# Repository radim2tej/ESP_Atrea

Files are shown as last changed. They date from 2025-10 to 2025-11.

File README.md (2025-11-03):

# ESP Atrea #
Replacement of the CP 07 RD controller with the ESP8266 module for controlling the Atrea RB / RC / RK2 / RDH air handling units and similar using Home Assistant. The module can either monitor or directly replace the CP07 controller via ESP8266, LIN bus interface and a Home Assistant. The module allows control of ventilation, heating and cooling.
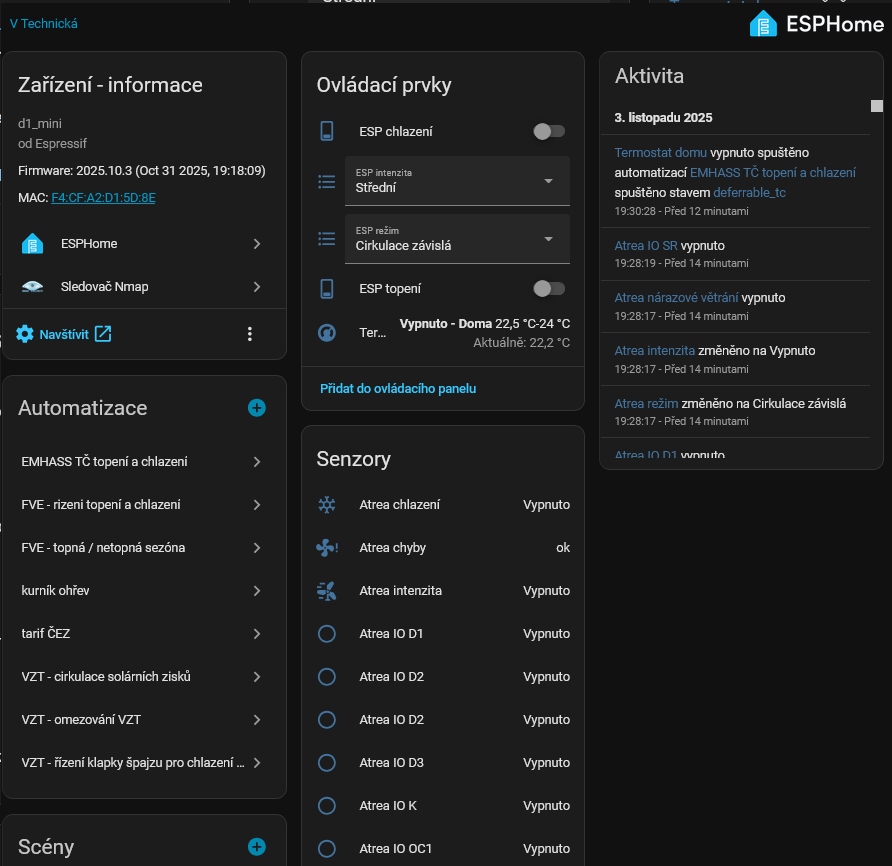
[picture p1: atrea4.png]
device


# Hardware
The CP07 controller communicates with the ATREA RK2 heat recovery unit via the LIN bus. It communicates at 300 Bauds and each packet has 10 bytes. The CP07 controller sends a query to the Atrea unit (the type is in bytes 2 and 3) and receives a response from Atrea.

For the connection use a LIN bus interface [TTL UART to LIN Can Bus Converter](https://www.aliexpress.com/item/1005006301070554.html) or maybe [UART to LIN Bus Module](https://www.aliexpress.com/item/1005008689817215.html), an ESP8266 module WeMos D1 mini and [DC Power Shield V1.1.0 for WEMOS D1 mini](https://www.aliexpress.com/item/1005001621800502.html).
The ESPAtrea module can completely replace the CP07 controller, but I recommend only inserting the module into the wiring and disconnecting the LINBUS wire to the CP07 controller with a switch due to the possibility of setting parameters. If the CP07 controller is connected and communicating, the ESPAtrea module detects this and only monitors the communication. The CP07 driver is still required to configure the unit, but can be disconnect after setup ATREA.

The complete module can be installed in a [printed box](espatrea.stl) with WAGO terminals. There is also space for installing a LINBUS switch for CP07.

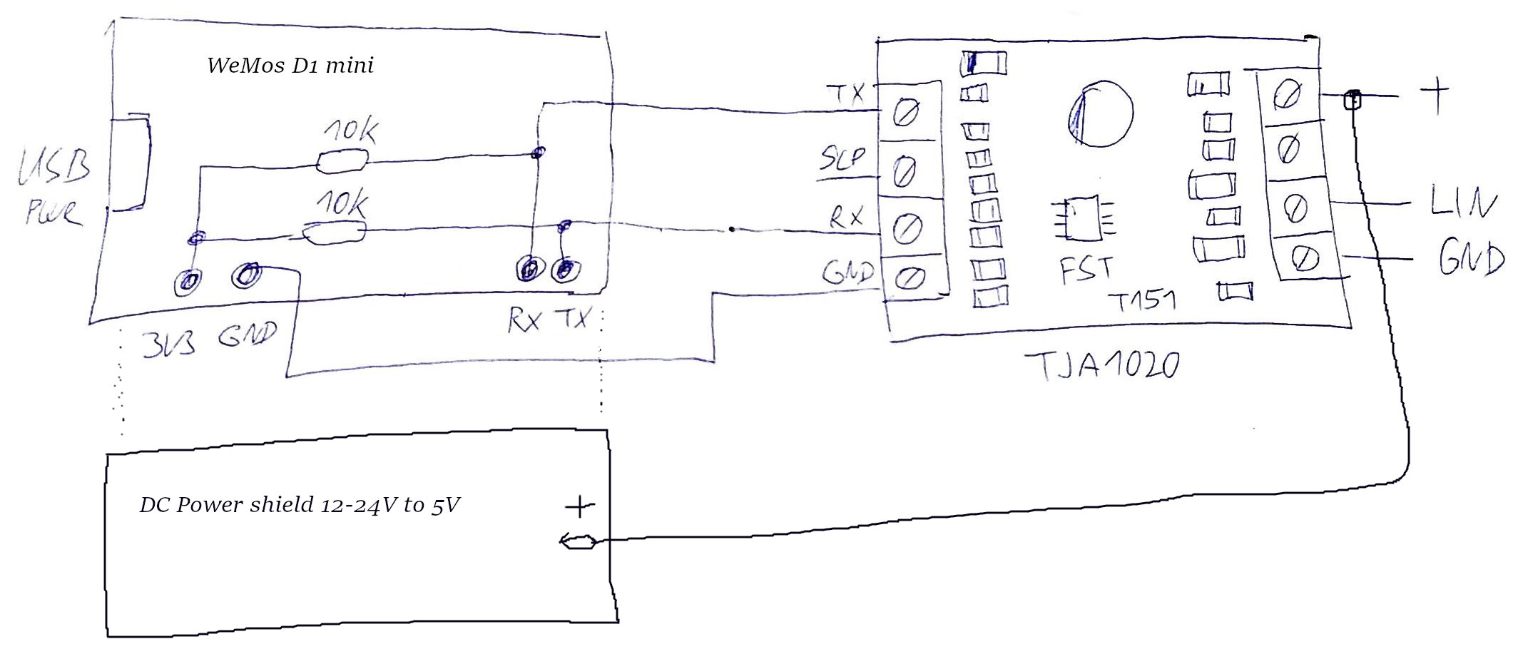
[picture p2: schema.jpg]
schema

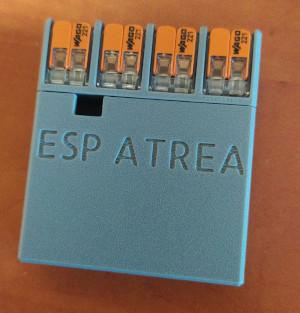
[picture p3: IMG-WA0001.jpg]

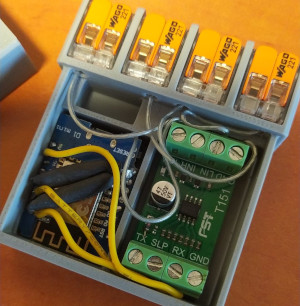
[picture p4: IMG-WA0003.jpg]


# Logs CP07 (fw 54.07) <-> Atrea (PIC fw 53.59 for Heating pump)
[Logs for individual modes](log.md)

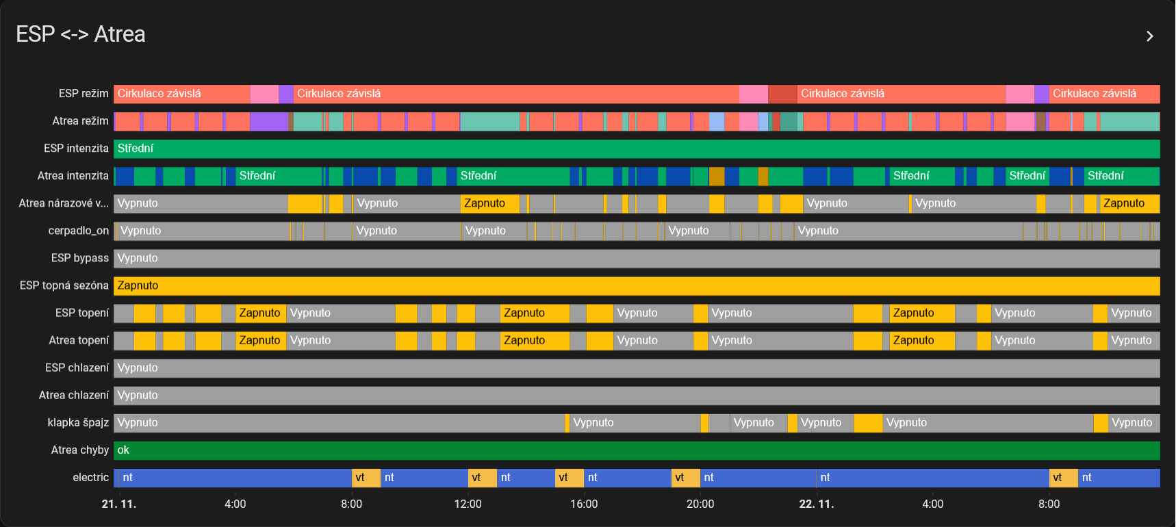
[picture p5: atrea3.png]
panel 1


# Decode packets
### The requests packet from the CP07 controller to the Atrea unit:
- 0xF5 [id1 0,1,2] [id2 1,3] [intensity 1,2,4] [mode 1,2,4,8,16] [bps 1,2] [md 1,2] [temp 0,1,2,3] 0x00 [crc]
  - id1 and id2: 0 1, 0 3, 1 3, 2 3
  - intensity is 1=off, 2=medium or 4=max
  - modes:
    - pressure ventilation (PV): mode = 1, bps = 2, md = 1, temp = 0
    - circulation (C): mode = 4, bps = 2, md = 1, temp = 0,2,3
    - dependent circulation (CZ): mode = 4, bps = 2, md = 2, temp = 0,2,3
    - circulation ventilation (CV): mode = 8, bps = 1,2, md = 1, temp = 0,2,3
    - equal pressure ventilation (RV): mode = 16, bps = 1,2, md = 1, temp = 0,2,3
    - cooling: mode = 1, bps = 2, md = 2, temp = 0,1
  - bps: bypass flap for RV and CV (1 bypass, 2 recuperator), in other modes is 2 
  - temp: bit 0x01 = heating / cooling, bit 0x02 = heating season (for new fw CP07?)

- 0xF5 [id1 0x41,0x42,0x43] [id2 0x01] [circulation flap DA1] [node DA2] [MC] [MV] [bits] 0x00 [crc]
  - simul. voltage intake circulation flap DA1: 0-255=0V-10V (adding fresh air 0-0%, 255-100%)
  - simul. voltage node DA2: 0-255=0V-10V
  - engine MC: 0,1,2,3
  - engine MV: 0,1,2
  - bits: 1=bypass SB, 2=ground cooler/intake flap SR (for input E1), 4=pump YV (heat pump heating), 8=electric/gas boiler K, 16=output OC1 (heat pump cooling), 32=output EXT

### The responds packet with the same id1 and id2 from the Atrea unit to the CP07 controller:
- 0xF5 [id1 0x00] [id2 0x01] [mode2 0,1,2,4,5,8,16] [flags: intensity 0,1,2, errorB 0x04, heating 0x08, shock vent. 0x10, fx 0x20] [errors] [TE] [TA] x [crc]
  - modes:
    - nothing: mode2 = 0, flags = 0 or 0x20
    - pressure ventilation: mode2 = 1, flags = 1 or 2
    - circulation: mode2 = 4, flag = 1 or 2
    - dependent circulation standby: mode2 = 4, flags = 0x20
    - dependent circulation ventilation: mode2 = 8, flags = 0x21 or 0x22
    - circulation ventilation: mode2 = 8, flag = 1 or 2xxx
    - equal pressure ventilation: mode2 = 16, flag = 0x21 or 0x22 (electric/gas boiler heating)
    - cooling: mode2 = 5, flags = 0x21 or 0x22
    - heating: mode2 = 4 (circulation dep. and circulation), 8 (circulation vent.), 16 (equal press. vent.), flags = 1 or 2 + 0x08 + fx
  - intensity: 0=off, 1=medium or 2=max
  - shock ventilation flag 0x10 (0x31 or 0x32 with intensity 1 or 2)
  - fx: RV 0 or 0x20 (keeps the previous state), CV 0 or 0x20 (keeps the previous state), CZ 0x20, C 0, PV 0, Cooling 0x20
  - errorB: 0x04 = filter clogged
  - errors: 1=TE error, 2=TI2 error, 4=recuperator freezing, 8=TA error, 16=1st.freezing protection (TI2 < 12°C), 32=2nd.freezing protection (TI2 < 7°C), 64=active STOP, 128=communication error
  - outdoor temperature = TE-50
  - radiator temperature = TA-50

- 0xF5 [id1 0x00] [id2 0x03] [0x60 + power inputs D1-D4 1,2,4,8] [mode] [i1 0x00] [i2 0x00] [i3 0x00] [bits] [crc]
  - power inputs: D1-D3 WC and bathroom 1,2,4, D4 kitchen 8, D11 ?
  - mode: 0=off, 2=PV medium or C medium, 3=PV max or C max, 5=RV medium, 10=RV max or shock ventilation, 6=CV medium, 7=CV max
  - i1-i3: I thing voltage in1-in3 0-255=0V-10V
  - bits: 1=ground cooler/intake flap SR (for input E1), 2=bypass SB, 4=pump YV (heat pump heating), 8=electric/gas boiler K, 32=output OC1 (heat pump cooling)
 
- 0xF5 [id1 0x01] [id2 0x03] [circulation flap DA1] [TA] [TI2] [TE] 0x00 0x99 [crc]
  - intake circulation flap DA1 0-255=0V-10V (adding fresh air 0-0%, 255-100%)
  - radiator temperature = TA-50
  - behind recuperator temperature = TI2-50
  - outdoor temperature = TE-50

- 0xF5 [id1 0x02] [id2 0x03] 0xFF 0x33 0x82 0xEC 0xFF 0xCB [crc]
  
- 0xF5 [id1 0x41] [id2 0x01] [TA] [TI2] [TE] 0x00 0x00 0x00 [crc]
  - radiator temperature = TA
  - behind recuperator temperature = TI2
  - outdoor temperature = TE
      
- 0xF5 [id1 0x42] [id2 0x01] 0xFF 0x33 0x82 0xEC 0xFF 0x0B [crc]
  
- 0xF5 [id1 0x43] [id2 0x01] 0x03 [D1..4] 0x00 0x00 0x00 0x00 [crc]
  - D1..4: D1-D3 WC and bathroom 2,4,8, D4 kitchen 16

### Byte bps control with CP07 controller
The Bps byte control the bypass flap - 1 for bypass and 2 for recuperator. In RV and CV mode, the CP07 controller sets the byte bps according to the outdoor TE temperature, room temperature, and target setpoint temperature. In other modes, the byte bps is set to 2.
#### Rules:
- for a heating season and active heating the CP07 controller sets bps to 2 
- for the heating season, not heating and RV mode
  - 1 = the outdoor TE temperature is greater or equal than 18°C and both the outdoor TE temperature and the requested indoor temperature are less than the actual room temperature
  - 2 = the outdoor TE temperature is less than 17°C or the outdoor TE temperature is greater than the actual room temperature or the requested indoor temperature is greater than the actual room temperature
- for the heating season, not heating and CV mode
  - 1 = the outdoor TE temperature is greater or equal than 16°C and both the outdoor TE temperature and the requested indoor temperature are less than the actual room temperature
  - 2 = the outdoor TE temperature is less than 15°C or the outdoor TE temperature is greater than the actual room temperature or the requested indoor temperature is greater than the actual room temperature
- for the non-heating season and RV mode
  - 1 = the outdoor TE temperature is greater or equal than 16°C and both the outdoor TE temperature and the requested indoor temperature are less than the actual room temperature
  - 2 = the outdoor TE temperature is less than 15°C or the outdoor TE temperature is greater than the actual room temperature or the requested indoor temperature is greater than the actual room temperature
- for the non-heating season and CV mode
  - 1 = the outdoor TE temperature is greater or equal than 13°C and both the outdoor TE temperature and the requested indoor temperature are less than the actual room temperature
  - 2 = the outdoor TE temperature is less than 12°C or the outdoor TE temperature is greater than the actual room temperature or the requested indoor temperature is greater than the actual room temperature

# Instalation
Programming of the module uses the ESPHome 2025 environment. The code is written in C and in YAML (espatrea.yaml and files in components/atrea). The files are moved to configuration/esphome. The wifi password is in secrets.yaml . In espatrea.yaml, edit the API Key and OTA and Wifi passwords. The module contains a software dual thermostat, and the current temperature is set by the home assistant via the sensor sensor.teplota_termostatu. The thermostat controls the switches switch.esp_topení and switch.esp_chlazeni.

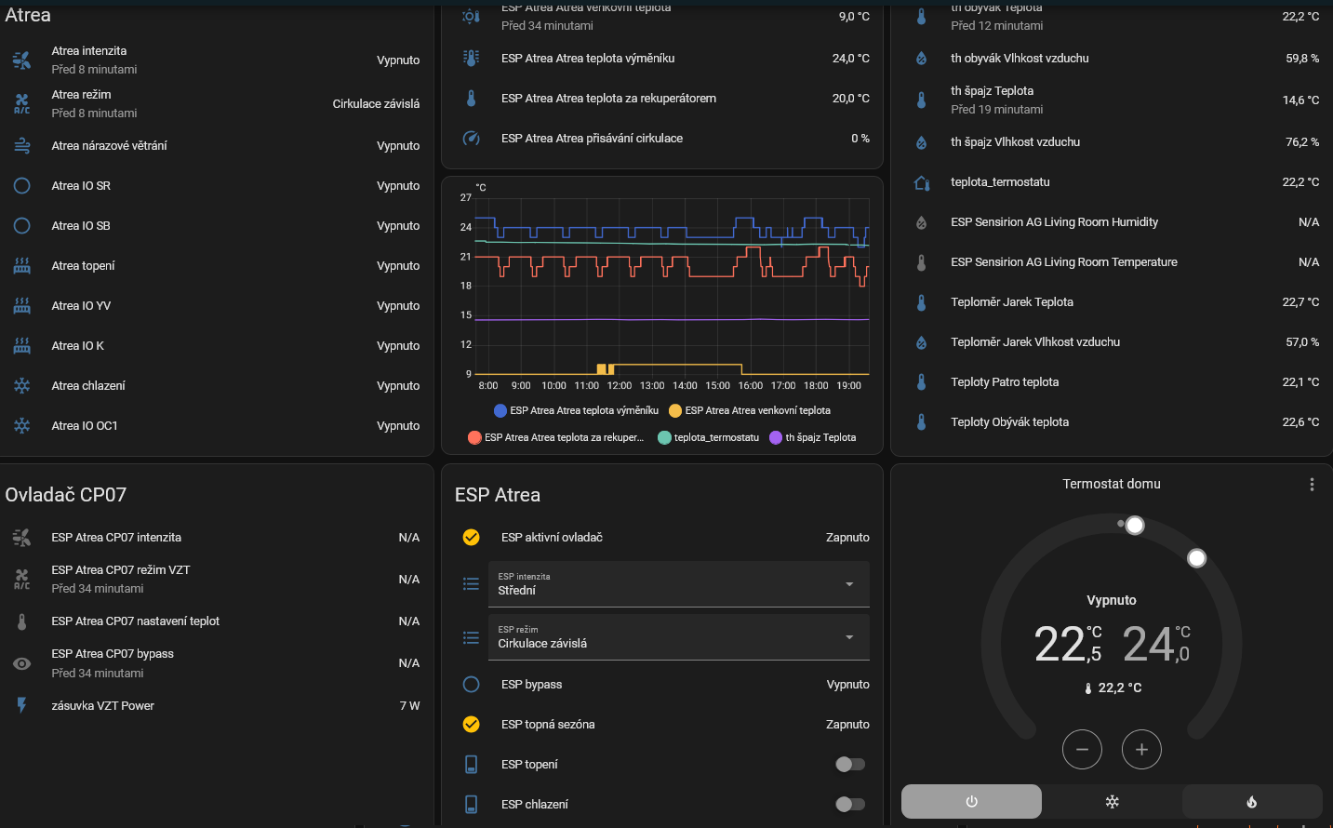
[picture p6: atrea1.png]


The unit modes can be selected via select.esp_rezim_vzt and select.esp_intenzita, and you can use scheduler to change modes due to different programs for individual days. Usually the unit runs in CZ mode, switches to RV in the morning and then to CV. Then it runs in CZ mode until the evening and then switches to RV, then to C and then to CZ. It varies by day of the week.

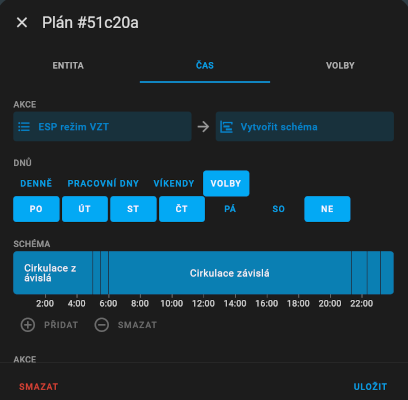
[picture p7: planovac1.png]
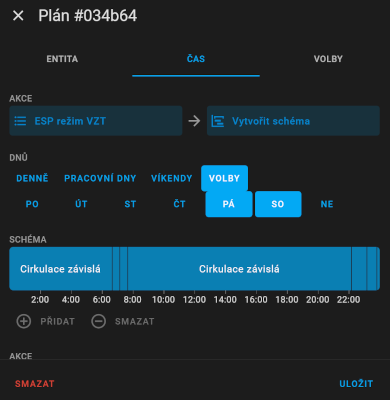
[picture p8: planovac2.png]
 

# Examples of automations
Solar gain circulation
```
alias: VZT - cirkulace solárních zisků
description: ""
triggers:
  - entity_id:
      - sun.sun
    attribute: elevation
    trigger: state
  - entity_id: sensor.pv_power
    for:
      hours: 0
      minutes: 10
      seconds: 0
    above: 2500
    enabled: false
    trigger: numeric_state
conditions:
  - condition: numeric_state
    entity_id: sun.sun
    attribute: elevation
    above: 14
actions:
  - if:
      - condition: numeric_state
        entity_id: sun.sun
        attribute: elevation
        above: 16
      - condition: numeric_state
        entity_id: climate.termostat_domu
        attribute: target_temp_high
        below: sensor.teplota_termostatu
    then:
      - action: select.select_option
        metadata: {}
        data:
          option: Cirkulace
        target:
          entity_id: select.esp_rezim_vzt
      - action: select.select_option
        metadata: {}
        data:
          option: Maximální
        target:
          entity_id: select.esp_intenzita
    else:
      - action: select.select_option
        metadata: {}
        data:
          option: Cirkulace závislá
        target:
          entity_id: select.esp_rezim_vzt
      - action: select.select_option
        metadata: {}
        data:
          option: Střední
        target:
          entity_id: select.esp_intenzita
mode: single
```

Control heating and cooling
```
alias: VZT - rizeni topení a chlazení
description: >-
  VZT nastavování teploty topení, blokování topení podle ceny, chlazení při
  nadbytku FVE
trigger:
  - platform: state
    entity_id:
      - sensor.final_price_kwh
    for:
      hours: 0
      minutes: 0
      seconds: 0
  - platform: state
    entity_id:
      - binary_sensor.atrea_narazove_vetrani
  - platform: time_pattern
    minutes: /20
    seconds: "5"
action:
  - alias: topení
    if:
      - condition: state
        entity_id: climate.termostat_domu
        state: heat
    then:
      - if:
          - condition: or
            conditions:
              - condition: state
                entity_id: binary_sensor.count_offpeak_heat_cheapest_hours
                state: "on"
              - condition: state
                entity_id: binary_sensor.count_peak_heat_cheapest_hours
                state: "on"
        then:
          - action: climate.set_temperature
            metadata: {}
            data:
              target_temp_low: 22
              target_temp_high: 24
            target:
              entity_id: climate.termostat_domu
        else:
          - if:
              - condition: state
                entity_id: binary_sensor.count_expensive_hours
                state: "on"
            then:
              - action: climate.set_temperature
                metadata: {}
                data:
                  target_temp_low: 20.5
                  target_temp_high: 24
                target:
                  entity_id: climate.termostat_domu
            else:
              - action: climate.set_temperature
                metadata: {}
                data:
                  target_temp_low: 21.5
                  target_temp_high: 24
                target:
                  entity_id: climate.termostat_domu
    else:
      - alias: kontrola nadbytku energie pro chlazeni
        if:
          - condition: and
            conditions:
              - condition: or
                conditions:
                  - condition: numeric_state
                    entity_id: sensor.pv_power
                    above: 2800
                  - condition: numeric_state
                    entity_id: sensor.export_s_tc
                    above: 900
              - condition: numeric_state
                entity_id: sensor.battery_state_of_charge
                above: 50
              - condition: numeric_state
                entity_id: sensor.solcast_pv_forecast_forecast_remaining_today
                below: sensor.battery_state_of_charge
                value_template: >-
                  {{ max(130 - 100 *
                  states('sensor.solcast_pv_forecast_forecast_remaining_today')
                  | float(default=50.0) / 14.4, 0) }}
                alias: bude větší výroba energie FVE k dobití baterie do 100%
              - condition: state
                entity_id: binary_sensor.chladici_sezona
                state: "on"
        then:
          - data:
              hvac_mode: cool
            target:
              entity_id: climate.termostat_domu
            action: climate.set_hvac_mode
          - device_id: 904cd0b7d9147d7b3b4ad392bb80d9a8
            domain: select
            entity_id: select.esp_intenzita
            type: select_option
            option: Maximální
            enabled: false
        else:
          - data:
              hvac_mode: "off"
            target:
              entity_id: climate.termostat_domu
            action: climate.set_hvac_mode
          - device_id: 904cd0b7d9147d7b3b4ad392bb80d9a8
            domain: select
            entity_id: select.esp_intenzita
            type: select_option
            option: Střední
            enabled: false
mode: single
```

Control heatin and cooling bypass
```
alias: VZT - řízení klapky špajzu pro chlazení / topení
description: chlazení a topení ve špajzu
triggers:
  - entity_id:
      - binary_sensor.atrea_chlazeni
    for:
      hours: 0
      minutes: 1
      seconds: 0
    trigger: state
  - entity_id:
      - binary_sensor.atrea_topeni
    for:
      hours: 0
      minutes: 1
      seconds: 0
    trigger: state
  - minutes: /10
    trigger: time_pattern
conditions: []
actions:
  - if:
      - condition: or
        conditions:
          - condition: state
            entity_id: binary_sensor.atrea_chlazeni
            state: "on"
          - condition: and
            conditions:
              - condition: or
                conditions:
                  - condition: state
                    entity_id: binary_sensor.atrea_topeni
                    state: "on"
                  - condition: state
                    entity_id: select.esp_rezim_vzt
                    state: Cirkulace
              - condition: numeric_state
                entity_id: sensor.th_spajz_teplota
                below: 10
    then:
      - type: turn_on
        device_id: 7b6b2b2705a9a6d467216a1d3fba84c2
        entity_id: light.klapka_spajz_vypinac
        domain: light
      - type: turn_on
        device_id: 7b6b2b2705a9a6d467216a1d3fba84c2
        entity_id: light.klapka_spajz_vypinac_2
        domain: light
    else:
      - type: turn_off
        device_id: 7b6b2b2705a9a6d467216a1d3fba84c2
        entity_id: light.klapka_spajz_vypinac
        domain: light
      - type: turn_off
        device_id: 7b6b2b2705a9a6d467216a1d3fba84c2
        entity_id: light.klapka_spajz_vypinac_2
        domain: light
mode: single
```

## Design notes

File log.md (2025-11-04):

# Logs CP 07 (fw 54.07) <-> Atrea RK2 (PIC fw 53.59 for Heating pump)
## operating mode equal pressure ventilation (RV)
#### not heating season
    off ventilation
      [CP-07]: F5 00 01 01 10 02 01 00 00 7C
      [ATREA]: F5 00 01 00 00 00 3D 48 FB EC
    medium ventilation
      [CP-07]: F5 00 01 02 10 02 01 00 00 25 (F5 00 01 02 10 01 01 00 00 xx)
      [ATREA]: F5 00 01 10 01 00 3D 48 FB 7A
    max ventilation
      [CP-07]: F5 00 01 04 10 02 01 00 00 97 (F5 00 01 04 10 01 01 00 00 xx)
      [ATREA]: F5 00 01 10 02 00 3D 48 FB 34
    medium / max shock ventilation
      [ATREA]: F5 00 01 10 12 00 3B 45 FB 10
      [ATREA]: F5 00 01 10 32 00 3B 48 FB 61
#### heating season, not heating
    off ventilation
      [CP-07]: F5 00 01 01 10 02 01 02 00 ED 
      [ATREA]: F5 00 01 00 00 00 3D 47 FB F4
    medium ventilation
      [CP-07]: F5 00 01 02 10 02 01 02 00 B4 (F5 00 01 02 10 01 01 02 00 xx)
      [ATREA]: F5 00 01 10 01 00 3D 48 FB 7A
    max ventilation
      [CP-07]: F5 00 01 04 10 02 01 02 00 06 (F5 00 01 04 10 01 01 02 00 xx) 
      [ATREA]: F5 00 01 10 02 00 3D 47 FB 2C
    medium / max shock ventilation
      [ATREA]: F5 00 01 10 32 00 3C 48 FB 1B
#### heating season, heating
    off ventilation (nonsense)
      [CP-07]: F5 00 01 01 10 02 01 03 00 29  
      [ATREA]: F5 00 01 00 00 00 3D 49 FB 28
    medium ventilation
      [CP-07]: F5 00 01 02 10 02 01 03 00 70
      [ATREA]: F5 00 01 10 09 00 3D 49 FB 80    // electric boiler heating
      [ATREA]: F5 00 01 10 29 00 3C 59 FB 3F    // electric boiler heating
    max ventilation
      [CP-07]: F5 00 01 04 10 02 01 03 00 C2
      [ATREA]: F5 00 01 10 0A 00 3D 54 FB xx    // electric boiler heating
      [ATREA]: F5 00 01 10 2A 00 3C 5A FB 24    // electric boiler heating
    medium / max shock ventilation
      [ATREA]: F5 00 01 10 1A 00 3D 58 FB 9A    // electric boiler heating
      [ATREA]: F5 00 01 10 3A 00 3D 46 FB 52    // electric boiler heating

## operating mode circulation ventilation (CV)
#### not heating season
    off ventilation
      [CP-07]: F5 00 01 01 08 02 01 00 00 3E
      [ATREA]: F5 00 01 00 00 00 3B 47 FB xx
      [ATREA]: F5 00 01 00 20 00 3B 47 FB DD
    medium ventilation
      [CP-07]: F5 00 01 02 08 02 01 00 00 67 (F5 00 01 02 08 01 01 00 00 xx)
      [ATREA]: F5 00 01 08 01 00 3B 49 FB 95
    max ventilation
      [CP-07]: F5 00 01 04 08 02 01 00 00 D5 (F5 00 01 04 08 01 01 00 00 xx)
      [ATREA]: F5 00 01 08 02 00 3B 49 FB DB
    medium / max shock ventilation WC
      [ATREA]: F5 00 01 08 31 00 3B 47 FB CD
      [ATREA]: F5 00 01 08 32 00 3B 47 FB 83
    medium / max shock ventilation kitchen
      [ATREA]: F5 00 01 10 32 00 3B 47 FB 79    // RV mode
#### heating season, not heating 
    off ventilation
      [CP-07]: F5 00 01 01 08 02 01 02 00 AF 
      [ATREA]: F5 00 01 00 00 00 3D 48 FB EC
    medium ventilation
      [CP-07]: F5 00 01 02 08 02 01 02 00 F6 (F5 00 01 02 08 01 01 02 00 xx)
      [ATREA]: F5 00 01 08 01 00 3D 48 FB 80
    max ventilation
      [CP-07]: F5 00 01 04 08 02 01 02 00 44 (F5 00 01 04 08 01 01 02 00 xx)
      [ATREA]: F5 00 01 08 02 00 3D 48 FB CE
    medium / max shock ventilation WC
      [ATREA]: F5 00 01 08 11 00 3D 49 FB 38
      [ATREA]: F5 00 01 08 12 00 3D 49 FB 76
    medium / max shock ventilation kitchen
      [ATREA]: F5 00 01 10 12 00 3D 49 FB 8C    // RV mode
#### heating season, heating 
    off ventilation
      [CP-07]: F5 00 01 01 08 02 01 03 00 6B 
      [ATREA]: F5 00 01 00 00 00 3D 58 FB 00
    medium ventilation
      [CP-07]: F5 00 01 02 08 02 01 03 00 32
      [ATREA]: F5 00 01 08 09 00 3B 47 FB 77
    max ventilation
      [CP-07]: F5 00 01 04 08 02 01 03 00 80 
      [ATREA]: F5 00 01 08 0A 00 3D 5E FB B6
    medium / max shock ventilation WC
      [ATREA]: F5 00 01 08 19 00 3C 56 FB 59
      [ATREA]: F5 00 01 08 39 00 3C 54 FB 30
      [ATREA]: F5 00 01 08 1A 00 3C 58 FB CB
      [ATREA]: F5 00 01 08 3A 00 3C 56 FB EF
    medium / max shock ventilation kitchen
      [ATREA]: F5 00 01 10 1A 00 3D 49 FB B2    // RV mode, electric boiler heating
      [ATREA]: F5 00 01 10 3A 00 3C 49 FB E1    // RV mode, electric boiler heating

## operating mode dependent circulation (CZ)
#### not heating season
    off ventilation
      [CP-07]: F5 00 01 01 04 02 02 00 00 FB
      [ATREA]: F5 00 01 00 20 00 3B 47 FB DD
    medium ventilation
      [CP-07]: F5 00 01 02 04 02 02 00 00 A2
      [ATREA]: F5 00 01 04 20 00 3C 4B FB 36    // standby
      [ATREA]: F5 00 01 08 21 00 3E 4A FB 0D    // ventilation (CV mode)
    max ventilation
      [CP-07]: F5 00 01 04 04 02 02 00 00 10
      [ATREA]: F5 00 01 04 20 00 3B 4A FB 88    // standby
      [ATREA]: F5 00 01 08 22 00 3E 4A FB xx    // ventilation (CV mode)
    medium / max shock ventilation WC
      [ATREA]: F5 00 01 04 31 00 3B 49 FB 6C
      [ATREA]: F5 00 01 04 32 00 3B 49 FB 22
    medium / max shock ventilation kitchen
      [ATREA]: F5 00 01 10 32 00 3B 49 FB A5    // RV mode
#### heating season, not heating
    off ventilation
      [CP-07]: F5 00 01 01 04 02 02 02 00 6A 
      [ATREA]: F5 00 01 00 20 00 3D 4C FB 2F
    medium ventilation
      [CP-07]: F5 00 01 02 04 02 02 02 00 33 
      [ATREA]: F5 00 01 04 20 00 3C 4B FB 36    // standby
      [ATREA]: F5 00 01 08 21 00 3E 4A FB 0D    // ventilation (CV mode)
    max ventilation
      [CP-07]: F5 00 01 04 04 02 02 02 00 81 
      [ATREA]: F5 00 01 04 20 00 3C 4B FB 36    // standby
      [ATREA]: F5 00 01 08 22 00 3E 4A FB xx    // ventilation (CV mode)
    medium / max shock ventilation WC
      [ATREA]: F5 00 01 04 31 00 3C 4A FB 43
      [ATREA]: F5 00 01 04 32 00 3D 57 FB C3
    medium / max shock ventilation kitchen
      [ATREA]: F5 00 01 10 32 00 3C 49 FB DF    // RV mode
#### heating season, heating
    off ventilation
      [CP-07]: F5 00 01 01 04 02 02 03 00 AE 
      [ATREA]: F5 00 01 00 20 00 3D 58 FB F8
    medium ventilation
      [CP-07]: F5 00 01 02 04 02 02 03 00 F7 
      [ATREA]: F5 00 01 04 29 00 3D 57 FB CF    // standby
      [ATREA]:                                  // ventilation with heating
    max ventilation
      [CP-07]: F5 00 01 04 04 02 02 03 00 45 
      [ATREA]: F5 00 01 04 2A 00 3D 55 FB 10    // standby
      [ATREA]:                                  // ventilation with heating
    medium / max shock ventilation WC
      [ATREA]: F5 00 01 04 39 00 3C 53 FB 23
      [ATREA]: F5 00 01 04 3A 00 3D 55 FB 6C
    max shock ventilation kitchen      
      [ATREA]: F5 00 01 10 3A 00 3C 4E FB 8F    // RV mode, electric boiler heating

## operating mode circulation (C)
#### not heating season
    off ventilation
      [CP-07]: F5 00 01 01 04 02 01 00 00 1F
      [ATREA]: F5 00 01 00 00 00 3B 46 FB E1
    medium ventilation
      [CP-07]: F5 00 01 02 04 02 01 00 00 46
      [ATREA]: F5 00 01 04 01 00 3B 4A FB BD
    max ventilation
      [CP-07]: F5 00 01 04 04 02 01 00 00 F4
      [ATREA]: F5 00 01 04 02 00 3B 49 FB A6
    medium / max shock ventilation WC
      [ATREA]: F5 00 01 04 11 00 3B 48 FB 50
      [ATREA]: F5 00 01 04 12 00 3B 48 FB 1E
    medium / max shock ventilation kitchen
      [ATREA]: F5 00 01 10 12 00 3B 47 FB 81    // RV mode
#### heating season, not heating      
    off ventilation
      [CP-07]: F5 00 01 01 04 02 01 02 00 8E 
      [ATREA]: F5 00 01 00 00 00 3C 4C FB 7C
    medium ventilation
      [CP-07]: F5 00 01 02 04 02 01 02 00 D7 
      [ATREA]: F5 00 01 04 01 00 3C 4C FB 6D
    max ventilation
      [CP-07]: F5 00 01 04 04 02 01 02 00 65 
      [ATREA]: F5 00 01 04 02 00 3C 4B FB 4D
    medium / max shock ventilation Wc
      [ATREA]: F5 00 01 04 11 00 3D 4A FB 10
      [ATREA]: F5 00 01 04 12 00 3D 49 FB 0B
    medium / max shock ventilation kitchen
      [ATREA]: F5 00 01 10 12 00 3D 49 FB 8C    // RV mode
#### heating season, heating
    off ventilation
      [CP-07]: F5 00 01 01 04 02 01 03 00 4A 
      [ATREA]: F5 00 01 00 00 00 3C 5B FB FE
    medium ventilation
      [CP-07]: F5 00 01 02 04 02 01 03 00 13 
      [ATREA]: F5 00 01 04 09 00 3C 59 FB 40
    max ventilation
      [CP-07]: F5 00 01 04 04 02 01 03 00 A1 
      [ATREA]: F5 00 01 04 0A 00 3C 58 FB CA
    medium / max shock ventilation WC
      [ATREA]: F5 00 01 04 19 00 3D 4A FB 2E
      [ATREA]: F5 00 01 04 1A 00 3C 54 FB FB
    medium / max shock ventilation kitchen
      [ATREA]: F5 00 01 10 1A 00 3C 53 FB 12    // RV mode, electric boiler heating

## operating mode pressure ventilation (PV)
    off ventilation
      [CP-07]: F5 00 01 01 01 02 01 00 00 CD
      [ATREA]: F5 00 01 00 00 00 3B 46 FB E1
    medium ventilation
      [CP-07]: F5 00 01 02 01 02 01 00 00 94
      [ATREA]: F5 00 01 01 01 00 3B 49 FB 03
    max ventilation
      [CP-07]: F5 00 01 04 01 02 01 00 00 26
      [ATREA]: F5 00 01 01 02 00 3B 49 FB 4D
    medium / max shock ventilation
      [ATREA]: F5 00 01 01 11 00 3B 49 FB 7F
      [ATREA]: F5 00 01 01 12 00 3B 47 FB ED
      
## operating mode cooling
#### not cooling
    cooling off
      [CP-07]: F5 00 01 01 01 02 02 00 00 xx
      [ATREA]: F5 00 01 00 20 00 3B 44 FB 88
    medium cooling
      [CP-07]: F5 00 01 02 01 02 02 00 00 xx
      [ATREA]: F5 00 01 05 20 00 3D 42 FB xx
    max cooling
      [CP-07]: F5 00 01 04 01 02 02 00 00 xx
      [ATREA]: F5 00 01 05 20 00 3D 49 FB xx
    medium / max shock ventilation WC
      [ATREA]: F5 00 01 01 31 00 3B 49 FB 87
      [ATREA]: F5 00 01 01 32 00 3B 49 FB C9
    medium / max shock ventilation kitchen
      [ATREA]: F5 00 01 01 31 00 3B 44 FB 0E
#### cooling
    cooling off
      [CP-07]: F5 00 01 01 01 02 02 01 00 ED
      [ATREA]: F5 00 01 00 20 00 3B 44 FB 88
    medium cooling
      [CP-07]: F5 00 01 02 01 02 02 01 00 B4
      [ATREA]: F5 00 01 05 21 00 3D 42 FB D5
    max cooling
      [CP-07]: F5 00 01 04 01 02 02 01 00 06
      [ATREA]: F5 00 01 05 22 00 3D 49 FB B8
    off / medium / max shock ventilation WC
      [ATREA]: F5 00 01 10 32 00 3C 4A FB 8A
      [ATREA]: F5 00 01 01 31 00 3B 49 FB 87
      [ATREA]: F5 00 01 01 32 00 3B 49 FB C9
    medium / max shock ventilation kitchen
      [ATREA]: F5 00 01 01 31 00 3B 44 FB 0E

## servis
    main menu
      [CP-07]: F5 00 01 02 10 02 01 02 00 B4
      [ATREA]: F5 00 01 10 32 00 3D 43 FB 93
      [CP-07]: F5 00 03 02 10 02 01 02 00 CE
      [ATREA]: F5 00 03 61 0A 00 00 00 81 7A
      [CP-07]: F5 00 01 02 10 02 01 02 00 B4
      [ATREA]: F5 00 01 10 32 00 3D 43 FB 93
      [CP-07]: F5 01 03 02 10 02 01 02 00 8D
      [ATREA]: F5 01 03 FF 43 43 3D 00 A9 C6
      [CP-07]: F5 00 01 02 10 02 01 02 00 B4
      [ATREA]: F5 00 01 10 32 00 3D 43 FB 93
      [CP-07]: F5 02 03 02 10 02 01 02 00 48
      [ATREA]: F5 02 03 FF 33 82 EC FF FB 8C
    main menu / outputs control
      [CP-07]: F5 41 01 00 00 00 00 00 00 91
      [ATREA]: F5 41 01 12 11 0B 00 00 00 81
      [CP-07]: F5 42 01 00 00 00 00 00 00 54
      [ATREA]: F5 42 01 FF 33 82 EC FF 3B 75
      [CP-07]: F5 43 01 00 00 00 00 00 00 17
      [ATREA]: F5 43 01 03 02 00 00 00 00 CD
      
## startup sequence after switch-on power
    [CP-07]: F5 00 01 01 10 02 01 00 00 7C
    [CP-07]: F5 00 01 01 10 02 01 00 00 7C
    [ATREA]: F5 00 01 00 00 00 00 00 FB CF
    [CP-07]: F5 00 01 01 10 02 01 00 00 7C
    [ATREA]: F5 00 01 1F 0F 00 00 00 FB DF
    [CP-07]: F5 00 01 01 10 02 01 00 00 7C
    [ATREA]: F5 00 01 1F 0F 00 00 00 FB DF
    [CP-07]: F5 00 01 01 10 02 01 00 00 7C
    [ATREA]: F5 00 01 1F 0F 00 00 00 FB DF
    [CP-07]: F5 00 01 01 10 02 01 00 00 7C
    [ATREA]: F5 00 01 1F 0F 00 00 00 FB DF
    [CP-07]: F5 00 01 01 10 02 01 00 00 7C
    [ATREA]: F5 00 01 1F 0F 00 00 00 FB DF
    [CP-07]: F5 00 01 01 10 02 01 00 00 7C
    [ATREA]: F5 00 01 1F 0F 00 00 00 FB DF
    [CP-07]: F5 00 01 01 10 02 01 00 00 7C
    [ATREA]: F5 00 01 1F 0F 00 00 00 FB DF
    [CP-07]: F5 00 01 01 10 02 01 00 00 7C
    [ATREA]: F5 00 01 1F 0F 00 3E 4B FB 4D
    [CP-07]: F5 52 01 01 10 02 01 00 00 E7
    [ATREA]: F5 52 01 32 4B 0F 35 00 00 6B
    [CP-07]: F5 53 01 01 10 02 01 00 00 A4
    [ATREA]: F5 53 01 37 2D 19 30 00 00 4A
    [CP-07]: F5 54 01 01 10 02 01 00 00 74
    [ATREA]: F5 54 01 32 0A 01 FF 00 00 F0
    [CP-07]: F5 52 01 01 10 02 01 00 00 E7
    [ATREA]: F5 52 01 32 4B 0F 35 00 00 6B
    [CP-07]: F5 53 01 01 10 02 01 00 00 A4
    [ATREA]: F5 53 01 37 2D 19 30 00 00 4A
    [CP-07]: F5 54 01 01 10 02 01 00 00 74
    [ATREA]: F5 54 01 32 0A 01 FF 00 00 F0
    [CP-07]: F5 54 01 01 10 02 01 00 00 74
    [ATREA]: F5 54 01 32 0A 01 FF 00 00 F0

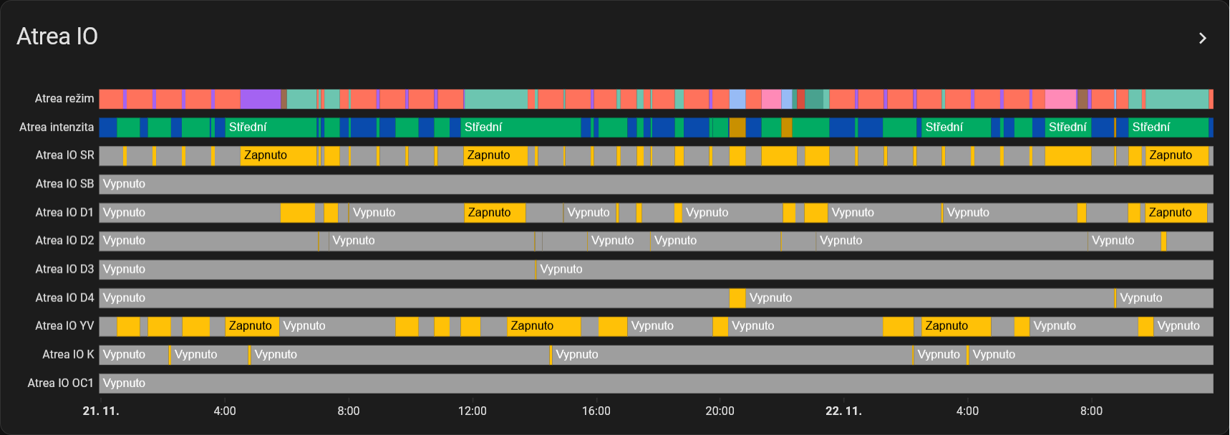
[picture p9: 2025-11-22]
atrea2.png

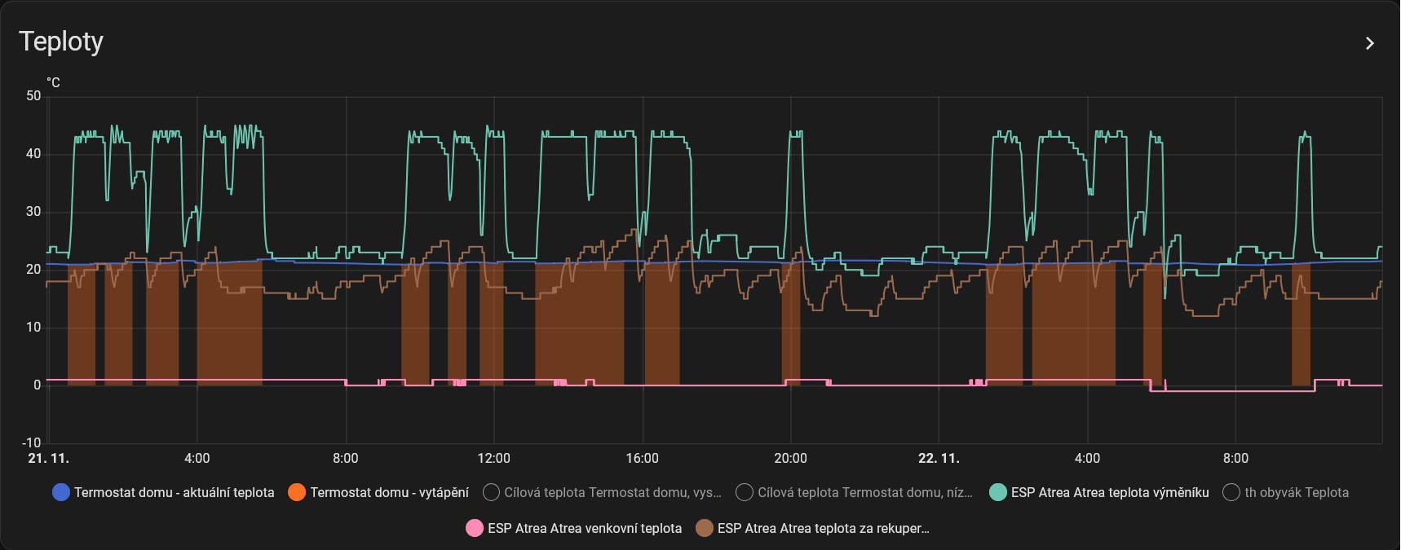
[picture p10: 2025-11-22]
atrea5.png

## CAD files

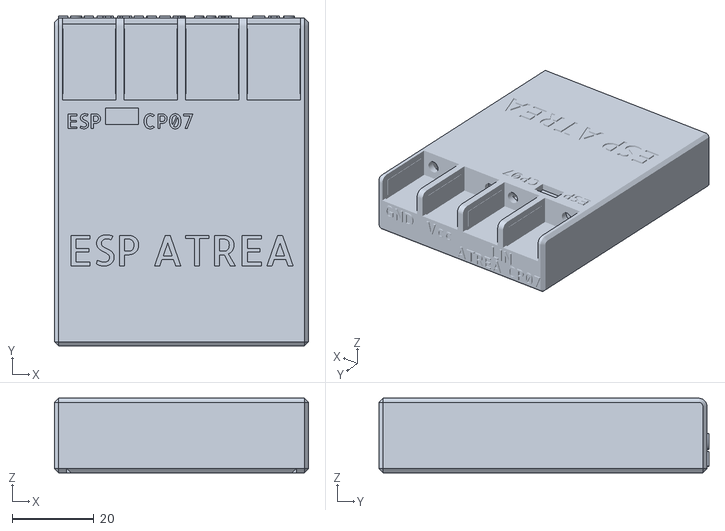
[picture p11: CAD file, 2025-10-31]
espatrea.stl
62.0 x 80.5 x 18.2

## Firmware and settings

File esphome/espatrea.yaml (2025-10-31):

esphome:
  name: espatrea
  platformio_options:
    build_flags:
      - -std=gnu++17

esp8266:
  board: d1_mini

# Enable logging
logger:
  hardware_uart: UART1
  level: DEBUG

# Enable Home Assistant API
api:
  encryption:
    key: "xxx"

ota:
  - platform: esphome
    password: "yyy"

wifi:
  ssid: !secret wifi_ssid
  password: !secret wifi_password
  ap:
    ssid: "ESPAtrea Fallback Hotspot"
    password: "zzz"
  manual_ip:
    static_ip: 192.168.1.204
    gateway: 192.168.1.1
    subnet: 255.255.255.0
  power_save_mode: none

captive_portal:

# External component configuration
external_components:
  - source:
      type: local
      path: components
    components: [ atrea ]

uart:
  id: uart_bus
  rx_pin: GPIO3
  tx_pin: GPIO1
  rx_buffer_size: 20
  baud_rate: 300

# Atrea component
atrea:
  id: atrea_component
  uart_id: uart_bus
  thermostat_id: termostat_domu
  esp_intensity_id: esp_intenzita
  esp_mode_id: esp_rezim_vzt
  esp_heating_id: esp_topeni
  esp_cooling_id: esp_chlazeni

# Text sensors
text_sensor:
  - platform: atrea
    atrea_id: atrea_component
    cp07_mode:
      name: "CP07 režim VZT"
      icon: "mdi:air-conditioner"
    cp07_intensity:
      name: "CP07 intenzita"
      icon: "mdi:wind-power"
    cp07_temperature_control:
      name: "CP07 nastavení teplot"
      icon: "mdi:thermometer"
    cp07_bypass:
      name: "CP07 bypass"
    atrea_mode:
      name: "Atrea režim VZT"
      icon: "mdi:air-conditioner"
    atrea_intensity:
      name: "Atrea intenzita"
      icon: "mdi:wind-power"
    atrea_errors:
      name: "Atrea chyby"
      icon: "mdi:fan-alert"

# Sensors
sensor:
  - platform: atrea
    atrea_id: atrea_component
    outdoor_temperature:
      name: "Atrea venkovní teplota"
      icon: "mdi:sun-thermometer-outline"
    exchanger_temperature:
      name: "Atrea teplota výměníku"
      icon: "mdi:thermometer-lines"
    recuperator_temperature:
      name: "Atrea teplota za rekuperátorem"
      icon: "mdi:thermometer"
    circulation:
      name: "Atrea přisávání cirkulace"
      icon: "mdi:speedometer"

  - platform: homeassistant
    id: esp_teplota_termostatu
    entity_id: sensor.teplota_termostatu
    unit_of_measurement: "°C"
    internal: true

# Binary sensors
binary_sensor:
  - platform: atrea
    atrea_id: atrea_component
    atrea_heating:
      name: "Atrea topení"
      icon: "mdi:radiator"
    atrea_cooling:
      name: "Atrea chlazení"
      icon: "mdi:snowflake"
    atrea_boost_ventilation:
      name: "Atrea nárazové větrání"
      icon: "mdi:weather-windy"
    atrea_d1:
      name: "Atrea IO vstup D1"
    atrea_d2:
      name: "Atrea IO vstup D2"
    atrea_d3:
      name: "Atrea IO vstup D3"
    atrea_d4:
      name: "Atrea IO vstup D4"
    atrea_damper_sr:
      name: "Atrea IO klapka sání SR"
    atrea_bypass_sb:
      name: "Atrea IO bypass SB"
    atrea_yv:
      name: "Atrea IO TČ topení YV"
    atrea_k:
      name: "Atrea IO kotel K"
    atrea_oc1:
      name: "Atrea IO TČ chlazení OC1"
    esp_active_controller:
      name: "ESP aktivní ovladač"
    esp_heating_season:
      name: "ESP topná sezóna"
    esp_bypass:
      name: "ESP bypass"

# Selects
select:
  - platform: template
    name: "ESP režim VZT"
    id: esp_rezim_vzt
    optimistic: true
    restore_value: true
    options:
      - "Rovnotlaké větrání"
      - "Cirkulační větrání"
      - "Cirkulace závislá"
      - "Cirkulace"
      - "Přetlakové větrání"
    initial_option: "Cirkulace závislá"
    
  - platform: template
    name: "ESP intenzita"
    id: esp_intenzita
    optimistic: true
    restore_value: true
    options:
      - Vypnuto
      - Střední
      - Maximální
    initial_option: "Střední"

# Switches
switch:
  - platform: template
    name: "ESP topení"
    id: esp_topeni
    optimistic: true
    turn_on_action:
      - switch.turn_off: esp_chlazeni
        
  - platform: template
    name: "ESP chlazení"
    id: esp_chlazeni
    optimistic: true
    turn_on_action:
      - switch.turn_off: esp_topeni
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
